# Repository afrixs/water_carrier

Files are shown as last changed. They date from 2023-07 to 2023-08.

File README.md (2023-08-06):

# water_carrier
A simple trail car for carrying liquids to be used by other robots.

## Objective
This is the first and simplest part of my larger conceptual project of a pipeless system that takes care of household (and possibly garden) plants at times when their owners are not at home. Currently the whole project is quite far from being complete, but you can find a simple working watering device [here](https://github.com/afrixs/plant-guard)

## Roadmap
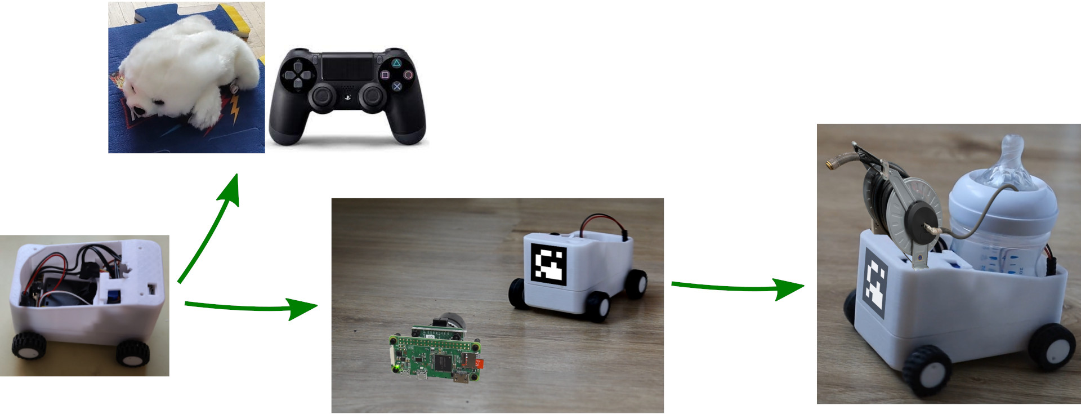
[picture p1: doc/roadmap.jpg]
Roadmap

 * Bluetooth-controlled robot body (Done)
 * [Gamepad-controlled toy](esp32/gamepad_toy/README.md) (Done)
 * Camera follower
 * Water carrier with a hose reel which can be controlled and used by other robots
 * Charging system, low battery alerts

### Current state
Water carrier v0.1 (https://www.youtube.com/watch?v=3kib8IhLip0)

## Shopping list
Giving links to sellers in Slovak/Czech market since I bought them here, but you can certainly find similar (or same) models and easily edit the corresponding dimensions in FreeCAD.

| Item | Link | Comment |
|---|---|---|
| ESP32 | [GME](https://www.gme.sk/v/1508256/esp-32s-24ghz-dual-mode-wifibluetooth) | |
| Voltage changer | [GME](https://www.gme.sk/v/1508405/modul-dc-dc-menic-step-down-125-32v-5a) | |
| DC Motors | [Techfun](https://techfun.sk/produkt/dc-motorcek-s-prevodom-rozne-typy/) [AliExpress](https://www.aliexpress.com/item/1005001340092317.html) | I used 6V/100RPM |
| DC Motors driver | [Techfun](https://techfun.sk/produkt/l9110s-dc-motor-driver-pre-4-motory/) | L9110S for 4 motors (2 for wheels, 1 for water pump) |
| Battery case | [GME](https://www.gme.sk/v/1506743/tg218650-dc21-drziak-baterie-2x18650) | |
| Batteries | [GME](https://www.gme.sk/v/1507017/panasonic-18650-li-ion-2900mah-akumulator) | 2x 18650 Li-ion 2900mAh |
| Voltage/current detection module | [GME](https://www.gme.sk/v/1507727/modul-merania-napatia-a-prudu-0-3a-a-3-25v) | In practice just a simple voltage divider is needed for low-battery alerts (which are not implemented yet by the way...) |
| + Power switch, connectors, cables, header strips ... (see photos) | | |
| Screws | | M3x8 Flat-head (4 for wheel tightening), M3x12 Flat-head + M3 nuts, 8x M1.6x4* (for holding wheel motors) |
| Wheels | [Lego](https://www.lego.com/en-us/product/telehandler-42133) | Lego wheels with 30.4mm diameter were used |

*Can be found in old cell-phones or maybe in laptops (also can be bought in some RC shops for 1 euro per screw :D). They need to be shorter than 5mm to avoid contact with gears (can be shortened by a file). Or a support part can be designed to hold the motors without screws - contributions are welcome.

<figure>
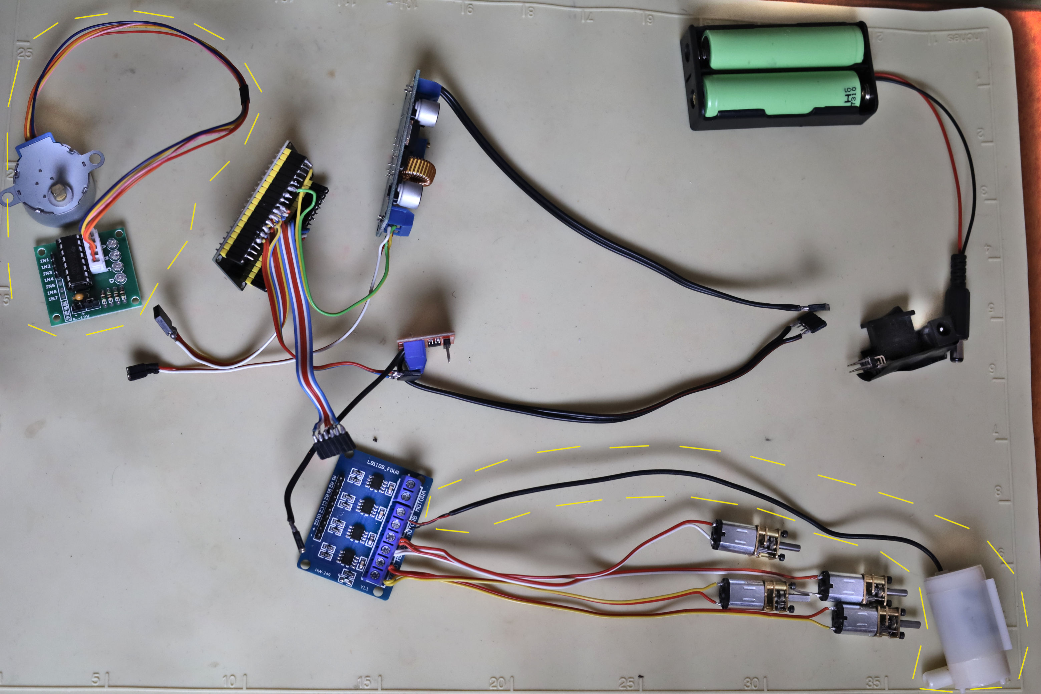
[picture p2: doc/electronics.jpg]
  
  <figcaption>Electronics used for robot. Yellow-dashed area - needed for next version (with hose reel + water pump + [water level sensor](https://www.hackster.io/mircemk/arduino-liquid-level-meter-with-simple-homemade-sensor-191413))</figcaption>
</figure>

<figure>
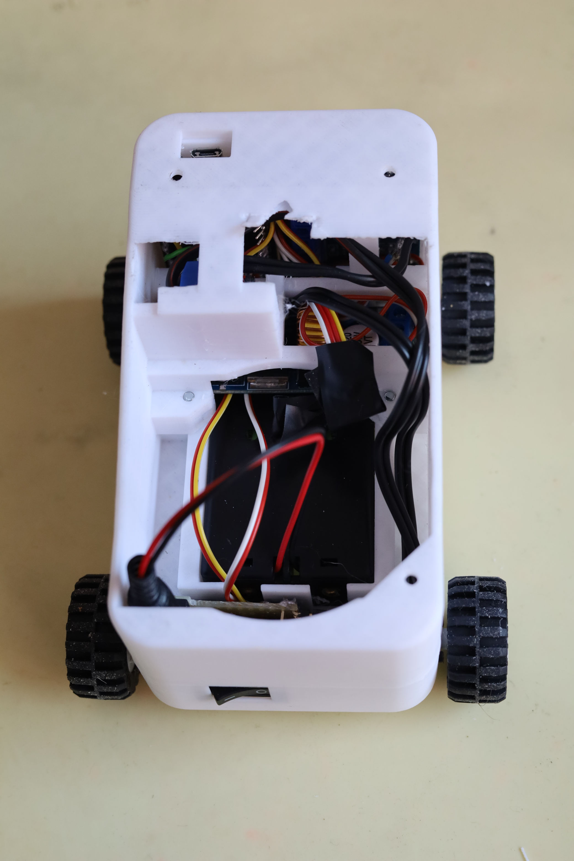
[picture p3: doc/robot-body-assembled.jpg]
  
  <figcaption>Assembled water_carrier robot v0.1</figcaption>
</figure>

## Installation
 * Set path to your `water_carrier/esp32` folder in *File -> Preferences -> Sketchbook location*
 * Add following to *File -> Preferences -> Additional boards manager* in your Arduino IDE
```
https://raw.githubusercontent.com/espressif/arduino-esp32/gh-pages/package_esp32_index.json
https://raw.githubusercontent.com/ricardoquesada/esp32-arduino-lib-builder/master/bluepad32_files/package_esp32_bluepad32_index.json
```
 * In *Tools -> Board -> Boards Manager* install *esp32* and *esp32_bluepad32* and select corresponding board in *Tools -> Board*, e.g.
   * *esp32 -> ESP32 Dev Module* for *water_carrier* 
   * *esp32_bluepad32 -> ESP32 Dev Module* for *gamepad_toy*
 * In *File -> Sketchbook* select *water_carrier* or *gamepad_toy*
 * Upload to your ESP32
 * For *water_carrier* control you can use a simple ROS2 [trail_control](ros/trail_control) node in combination with e.g. `ros2 run teleop_twist_keyboard teleop_twist_keyboard`

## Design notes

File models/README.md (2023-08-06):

# Models
These are models to be 3D-printed for the robot. Basically you need to print each `.3mf` file once.
I use [PrusaSlicer](https://www.prusa3d.com/) for slicing and generating gcode.

## Editing
Probably (unless you happen to collect exactly the same [components](../README.md#shopping-list) as me) you'll need to edit
some parts. Currently I suggest using [toponaming](https://github.com/FreeCAD/FreeCAD/tree/development/toponaming) branch of
FreeCAD and (to prevent headaches) **not mapping anything on 3D features**, i.e. project only geometry from sketches and
use DatumPlanes and parametric expressions to achieve proper structure, otherwise recomputing hell will come upon you
with refernces jumping from one feature to another etc.

After editing and exporting the models, there is a `Reload from disk` feature in PrusaSlicer. After reloading from disk you will want to add supports to all overhangs under 40˚ and to disable supports at specific places where they are not actually needed and are
hard to tear off after parts have been printed
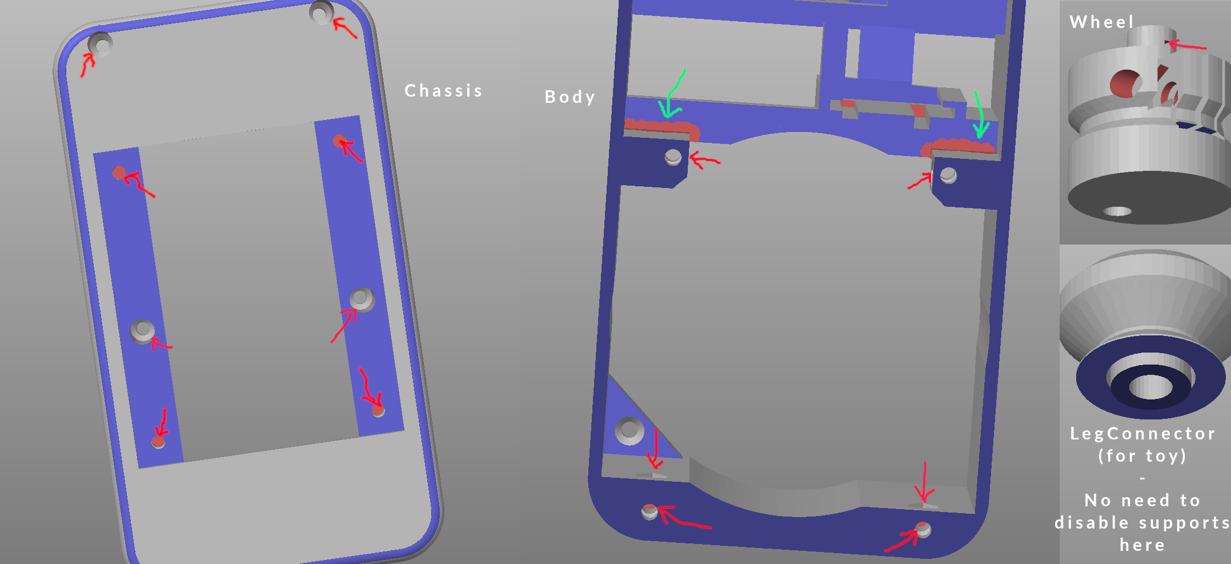
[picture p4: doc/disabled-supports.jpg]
Supports to be disabled

 * disabled surfaces are marked by red
 * some less visible surfaces are highlighted by red arrows
 * green arrows show areas that need to be also disabled to prevent support dilatation into problematic neighbouring pockets

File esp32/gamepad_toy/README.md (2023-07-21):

# Stuffed seal
A gamepad-controlled toy 

Robotic stuffed seal (https://www.youtube.com/watch?v=QQYB-n-5pwM)

## Objective
A large-scale DIY project needs some nice checkpoints on the road and this is one of them -
a cute stuffed toy for my daughter

## Manufacturing technique
It was just a long-lasting relaxing handwork, so there is not too much
work I can spare you from, so I'll just add steps of my work:
 * sewing a coat for [water_carrier](../../README.md) robot with an elastic band and holes for wheels
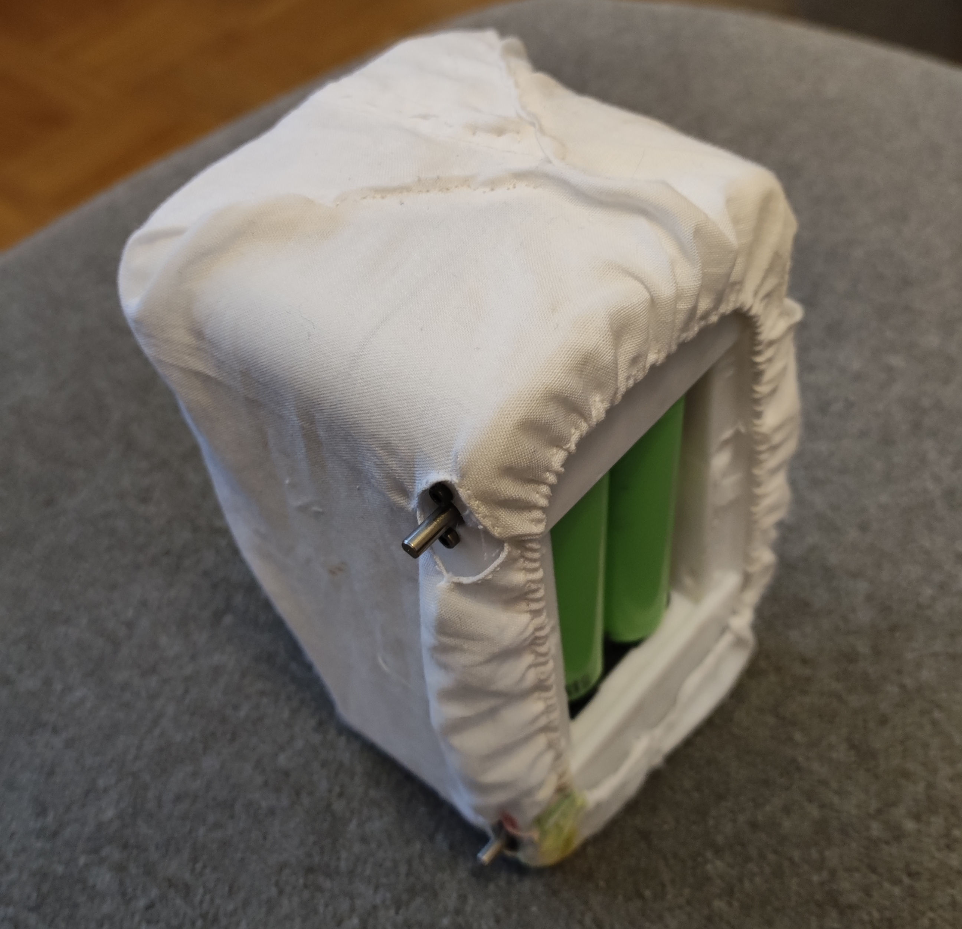
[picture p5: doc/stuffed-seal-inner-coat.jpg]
Stuffed seal inner coat
   

 * unstitching a stuffed animal toy (I used a seal, but maybe something as fat but with longer legs would be better,
   e.g. a hippo or a pig, so that the movement is clearer and motors are not burdened too much)
   and sewing it onto the coat
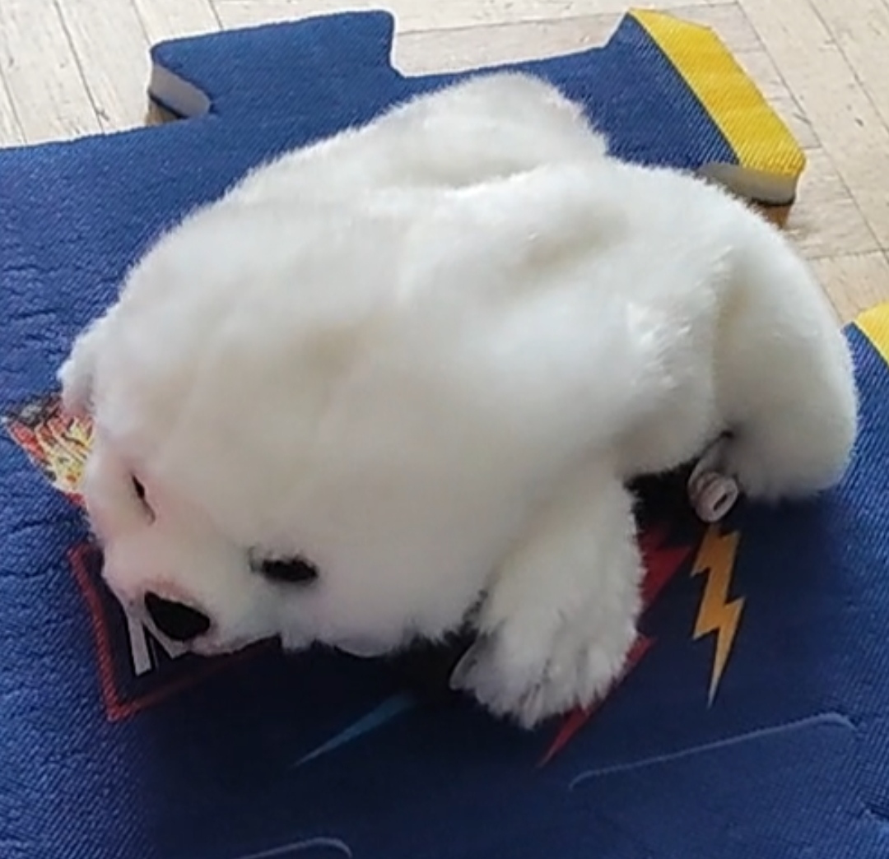
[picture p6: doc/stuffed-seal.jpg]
Stuffed seal
   

 * sewing rubber bands onto the feet of the toy and fixing them to the
   [LegConnectors](../../models/water_carrier-LegConnector.3mf) mounted on the wheels
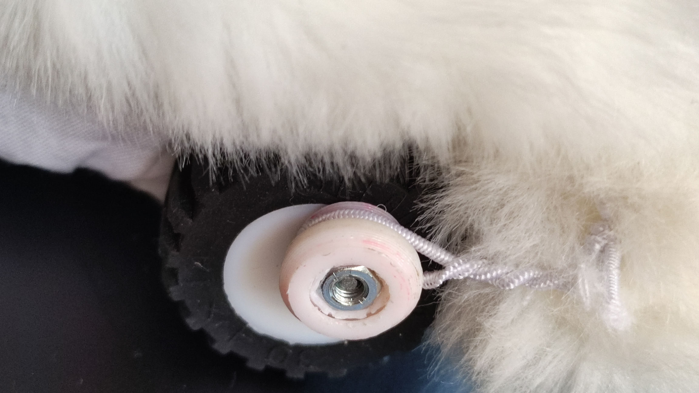
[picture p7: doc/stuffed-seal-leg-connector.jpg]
Stuffed seal


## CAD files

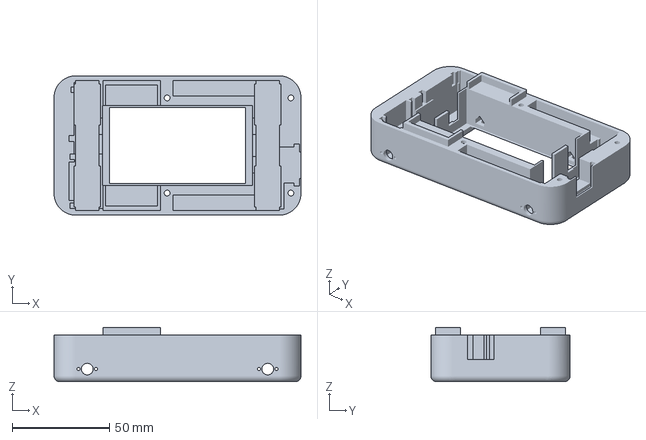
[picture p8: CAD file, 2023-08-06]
models/water_carrier-Chassis.3mf
127.3 x 71.8 x 28.0 mm

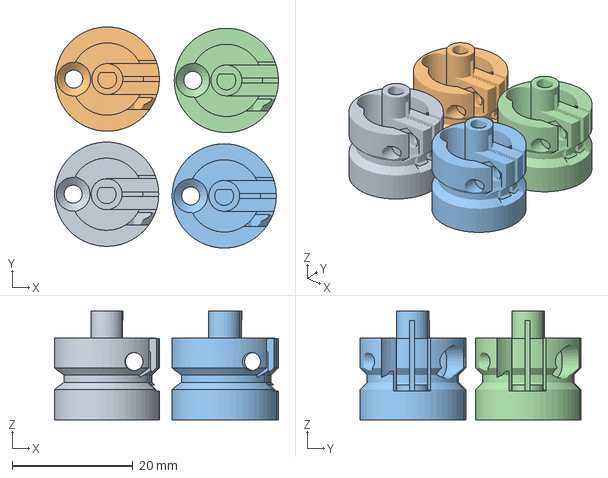
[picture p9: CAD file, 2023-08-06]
models/water_carrier-Wheel.3mf
37.2 x 36.7 x 18.0 mm
water_carrier-Wheel.stl x 4

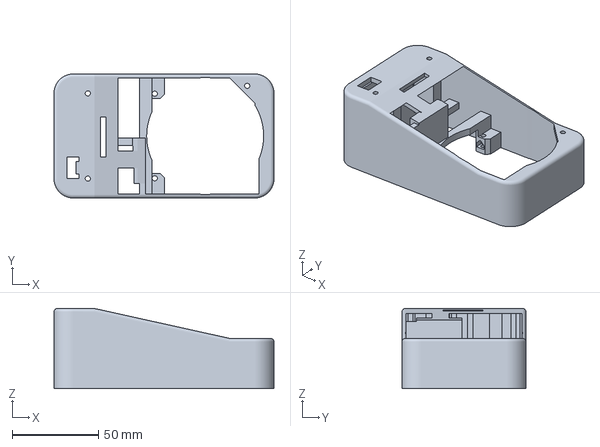
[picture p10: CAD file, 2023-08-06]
models/water_carrier-Body.3mf
127.3 x 71.8 x 46.4 mm

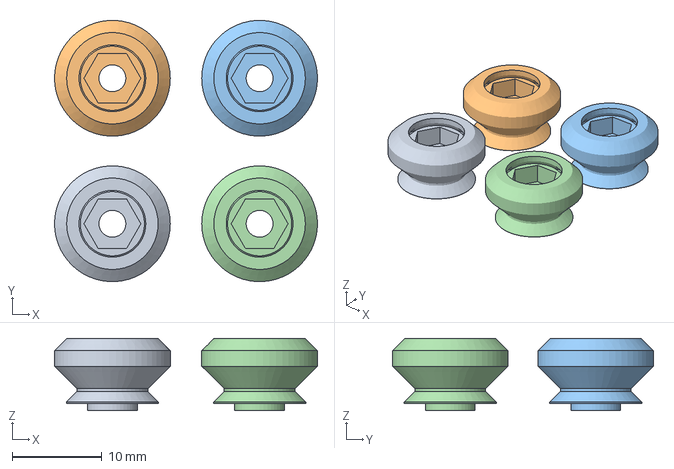
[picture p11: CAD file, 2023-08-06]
models/water_carrier-LegConnector.3mf
29.3 x 29.1 x 8.02 mm
water_carrier-LegConnector.stl x 4

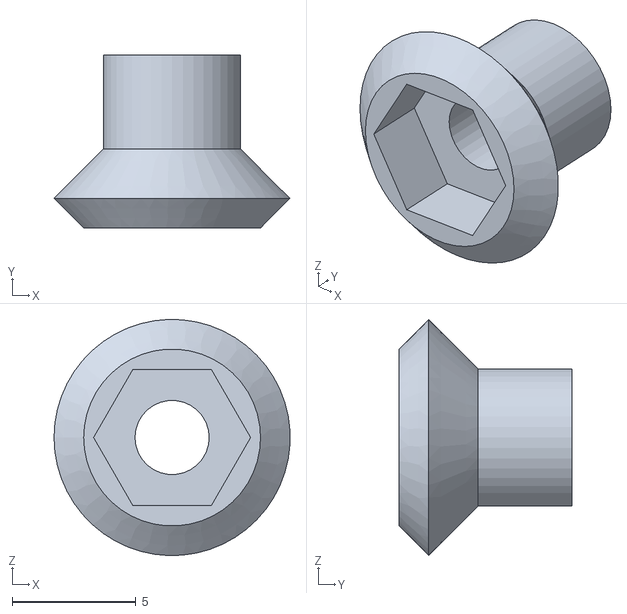
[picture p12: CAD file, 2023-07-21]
models/water_carrier-LegConnectorAxis.stl
9.54 x 7.00 x 9.55

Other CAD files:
models/water_carrier-Body.stl
models/water_carrier-Chassis.stl
models/water_carrier-LegConnector.stl
models/water_carrier-Wheel.stl

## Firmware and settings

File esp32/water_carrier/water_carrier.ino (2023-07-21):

// SPDX-FileCopyrightText: 2023 Matej Vargovcik <matej.vargovcik@gmail.com>
// SPDX-License-Identifier: MIT

// Based on ESP32 BLE Arduino/BLE_uart example which is
// - Based on Neil Kolban example for IDF: https://github.com/nkolban/esp32-snippets/blob/master/cpp_utils/tests/BLE%20Tests/SampleNotify.cpp
// - Ported to Arduino ESP32 by Evandro Copercini

#include "BluetoothSerial.h"
#include "dc_motor.h"

#if !defined(CONFIG_BT_ENABLED) || !defined(CONFIG_BLUEDROID_ENABLED)
#error Bluetooth is not enabled! Please run 'make menuconfig' to and enable it
#endif

BluetoothSerial SerialBT;

#include <BLEDevice.h>
#include <BLEServer.h>
#include <BLEUtils.h>
#include <BLE2902.h>

BLEServer *pServer = NULL;
BLECharacteristic * pTxCharacteristic;
bool deviceConnected = false;
bool oldDeviceConnected = false;
uint8_t txValue = 0;

// See the following for generating UUIDs:
// https://www.uuidgenerator.net/

#define SERVICE_UUID           "6E400001-B5A3-F393-E0A9-E50E24DCCA9E" // UART service UUID
#define CHARACTERISTIC_UUID_RX "6E400002-B5A3-F393-E0A9-E50E24DCCA9E"
#define CHARACTERISTIC_UUID_TX "6E400003-B5A3-F393-E0A9-E50E24DCCA9E"

bool readingRight = false;
String readStringLeft;
String readStringRight;

class MyServerCallbacks: public BLEServerCallbacks {
    void onConnect(BLEServer* pServer) {
      deviceConnected = true;
    };

    void onDisconnect(BLEServer* pServer) {
      deviceConnected = false;
    }
};

class MyCallbacks: public BLECharacteristicCallbacks {
    void onWrite(BLECharacteristic *pCharacteristic) {
      std::string rxValue = pCharacteristic->getValue();

      if (rxValue.length() > 0) {
        Serial.println("*********");
        Serial.print("Received Value: ");

        bool lineComplete = false;
        for (int i = 0; i < rxValue.length(); i++) {
          char c = rxValue[i];
          Serial.print(c);
          if (c == '\n') {
            lineComplete = true;
            readingRight = false;
            break;
          }
          else if (c == ' ')
            readingRight = true;
          else if (readingRight)
            readStringRight += c;
          else
            readStringLeft += c;
        }
        Serial.println();
        if (lineComplete) {
          double leftSpeed, rightSpeed;
          leftSpeed = readStringLeft.toDouble();
          rightSpeed = readStringRight.toDouble();

          // clamp to <-1..1> interval, keep ratio
          double maxSpeed = max(abs(leftSpeed), abs(rightSpeed));
          if (maxSpeed > 1.0) {
            leftSpeed /= maxSpeed;
            rightSpeed /= maxSpeed;
          }
          
          DCMotor::leftMotor.setSpeed(leftSpeed);
          DCMotor::rightMotor.setSpeed(-rightSpeed);
      
          Serial.print("Left: ");
          Serial.print(leftSpeed);
          Serial.print(", Right: ");
          Serial.println(rightSpeed);
      
          readStringLeft = "";
          readStringRight = "";
        }
        Serial.println("*********");
      }
    }
};

void setup() {
  Serial.begin(115200);
  Serial.println("Starting!");

  // Create the BLE Device

  BLEDevice::init("ESP32");

  // Create the BLE Server
  pServer = BLEDevice::createServer();
  pServer->setCallbacks(new MyServerCallbacks());

  // Create the BLE Service
  BLEService *pService = pServer->createService(SERVICE_UUID);

  // Create a BLE Characteristic
  pTxCharacteristic = pService->createCharacteristic(
                    CHARACTERISTIC_UUID_TX,
                    BLECharacteristic::PROPERTY_NOTIFY
                  );
                      
  pTxCharacteristic->addDescriptor(new BLE2902());

  BLECharacteristic * pRxCharacteristic = pService->createCharacteristic(
                       CHARACTERISTIC_UUID_RX,
                      BLECharacteristic::PROPERTY_WRITE
                    );

  pRxCharacteristic->setCallbacks(new MyCallbacks());

  // Start the service
  pService->start();

  // Start advertising
  pServer->getAdvertising()->start();
}

void loop() {
  // Send data
//  if (deviceConnected) {
//    pTxCharacteristic->setValue(&txValue, 1);
//    pTxCharacteristic->notify();
//    txValue++;
//    delay(10); // bluetooth stack will go into congestion, if too many packets are sent
//  }

  // disconnecting
  if (!deviceConnected && oldDeviceConnected) {
    delay(500); // give the bluetooth stack the chance to get things ready
    pServer->startAdvertising(); // restart advertising
    Serial.println("start advertising");
    oldDeviceConnected = deviceConnected;
  }
  // connecting
  if (deviceConnected && !oldDeviceConnected) {
    // do stuff here on connecting
    oldDeviceConnected = deviceConnected;
    Serial.println("Device connected");
  }
}

////////////////////////////// Stepper motor code //////////////////////////////////////
//// Include the AccelStepper Library
//#include <AccelStepper.h>
//
//// Define step constant
//#define MotorInterfaceType 4
//
//// Creates an instance
//// Pins entered in sequence IN1-IN3-IN2-IN4 for proper step sequence
//AccelStepper myStepper(MotorInterfaceType, 12, 15, 13, 14);
//
//void setup() {
//  Serial.begin(115200);
//  Serial.println("Hello");
//  // set the maximum speed, acceleration factor,
//  // initial speed and the target position
//  myStepper.setMaxSpeed(700.0);
//  myStepper.setAcceleration(1000.0);
//  myStepper.setSpeed(700);
//  myStepper.moveTo(2038);
//}
//
//void loop() {
//  // Change direction once the motor reaches target position
//  if (myStepper.distanceToGo() == 0) {
//    myStepper.moveTo(2038-myStepper.currentPosition());
//    Serial.println(myStepper.currentPosition());
//  }
////  Serial.println("dist:");
////  Serial.println(myStepper.distanceToGo());
////  Serial.println("cur:");
////  Serial.println(myStepper.currentPosition());
//
//  // Move the motor one step
////  delay(2000);
//  myStepper.run();
//}

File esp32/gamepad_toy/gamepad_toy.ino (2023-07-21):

// SPDX-FileCopyrightText: 2023 Matej Vargovcik <matej.vargovcik@gmail.com>
// SPDX-License-Identifier: MIT

// Arduino IDE setup for control with gamepad: https://gitlab.com/ricardoquesada/bluepad32/-/blob/main/docs/plat_arduino.md
// Based on Bluepad32/Controller example with
//  - Copyright 2021 - 2023, Ricardo Quesada
//  - SPDX-License-Identifier: Apache 2.0 or LGPL-2.1-or-later

#include <Bluepad32.h>
#include "dc_motor.h"

ControllerPtr gamepads[BP32_MAX_CONTROLLERS];

// This callback gets called any time a new gamepad is connected.
// Up to 4 gamepads can be connected at the same time.
void onConnectedController(ControllerPtr ctl) {
  bool foundEmptySlot = false;
  for (int i = 0; i < BP32_MAX_GAMEPADS; i++) {
    if (gamepads[i] == nullptr) {
      Serial.print("CALLBACK: Controller is connected, index=");
      Serial.println(i);
      gamepads[i] = ctl;
      foundEmptySlot = true;

      // Optional, once the gamepad is connected, request further info about the
      // gamepad.
      ControllerProperties properties = ctl->getProperties();
      char buf[80];
      sprintf(buf,
              "BTAddr: %02x:%02x:%02x:%02x:%02x:%02x, VID/PID: %04x:%04x, "
              "flags: 0x%02x",
              properties.btaddr[0], properties.btaddr[1], properties.btaddr[2],
              properties.btaddr[3], properties.btaddr[4], properties.btaddr[5],
              properties.vendor_id, properties.product_id, properties.flags);
      Serial.println(buf);
      break;
    }
  }
  if (!foundEmptySlot) {
    Serial.println(
        "CALLBACK: Controller connected, but could not found empty slot");
  }
}

void onDisconnectedController(ControllerPtr ctl) {
  bool foundGamepad = false;

  for (int i = 0; i < BP32_MAX_GAMEPADS; i++) {
    if (gamepads[i] == ctl) {
      Serial.print("CALLBACK: Controller is disconnected from index=");
      Serial.println(i);
      gamepads[i] = nullptr;
      foundGamepad = true;
      break;
    }
  }

  if (!foundGamepad) {
    Serial.println(
        "CALLBACK: Controller disconnected, but not found in gamepads");
  }
}

void processGamepad(ControllerPtr gamepad) {
  double linear_vel_x = -gamepad->axisY()/512.0;
  double angular_vel_z = -gamepad->axisX()/512.0;
  double leftSpeed = linear_vel_x - angular_vel_z;
  double rightSpeed = linear_vel_x + angular_vel_z;

    // clamp to <-1..1> interval, keep ratio
  double maxSpeed = max(abs(leftSpeed), abs(rightSpeed));
  if (maxSpeed > 1.0) {
    leftSpeed /= maxSpeed;
    rightSpeed /= maxSpeed;
  }
  
  DCMotor::leftMotor.setSpeed(leftSpeed);
  DCMotor::rightMotor.setSpeed(-rightSpeed);

  Serial.print("Left: ");
  Serial.print(leftSpeed);
  Serial.print(", Right: ");
  Serial.println(rightSpeed);
}

void setup() {
  Serial.begin(115200);
  Serial.println("Starting!");

  String fv = BP32.firmwareVersion();
  Serial.print("Firmware version installed: ");
  Serial.println(fv);

  // To get the BD Address (MAC address) call:
  const uint8_t* addr = BP32.localBdAddress();
  Serial.print("BD Address: ");
  for (int i = 0; i < 6; i++) {
    Serial.print(addr[i], HEX);
    if (i < 5)
      Serial.print(":");
    else
      Serial.println();
  }

  // BP32.pinMode(27, OUTPUT);
  // BP32.digitalWrite(27, 0);

  // This call is mandatory. It setups Bluepad32 and creates the callbacks.
  BP32.setup(&onConnectedController, &onDisconnectedController);

  // "forgetBluetoothKeys()" should be called when the user performs
  // a "device factory reset", or similar.
  // Calling "forgetBluetoothKeys" in setup() just as an example.
  // Forgetting Bluetooth keys prevents "paired" gamepads to reconnect.
  // But might also fix some connection / re-connection issues.
  BP32.forgetBluetoothKeys();
}

void loop() {
  BP32.update();

  // It is safe to always do this before using the controller API.
  // This guarantees that the controller is valid and connected.
  for (int i = 0; i < BP32_MAX_CONTROLLERS; i++) {
    ControllerPtr gamepad = gamepads[i];

    if (gamepad && gamepad->isConnected()) {
      if (gamepad->isGamepad())
        processGamepad(gamepad);
    }
  }
  delay(50);
}

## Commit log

2023-07-21 version 0.1
    basic robot body with wheels controllable via BLE or a bluetooth gamepad
    + stuffed seal toy
    [water_carrier-Body.3mf, water_carrier-Body.stl, water_carrier-Chassis.3mf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]
2023-08-06 changed absolute paths in 3mf files to relative
    [water_carrier-Body.3mf, water_carrier-Chassis.3mf, water_carrier-LegConnector.3mf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]
